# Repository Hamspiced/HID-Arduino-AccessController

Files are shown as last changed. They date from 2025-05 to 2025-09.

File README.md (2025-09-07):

# HID-Arduino-AccessController
This is a project repository for creating a full fledged door access controller using an HID Reader, Arduino, and i2c screen.  

The Arduino portion of this project will allow you to use the reader as a simple badge scanner, act as a door controller, identify authorized access control cards, add cards, and delete cards.

The ESP32 Portion of this project will do all of the same as well as connect to your wifi or host an AP that can be connected do.  Through the Web Server you can add an Admin card, trigger the door signal, add cards, remove cards, as well as see a log of all scanned cards.

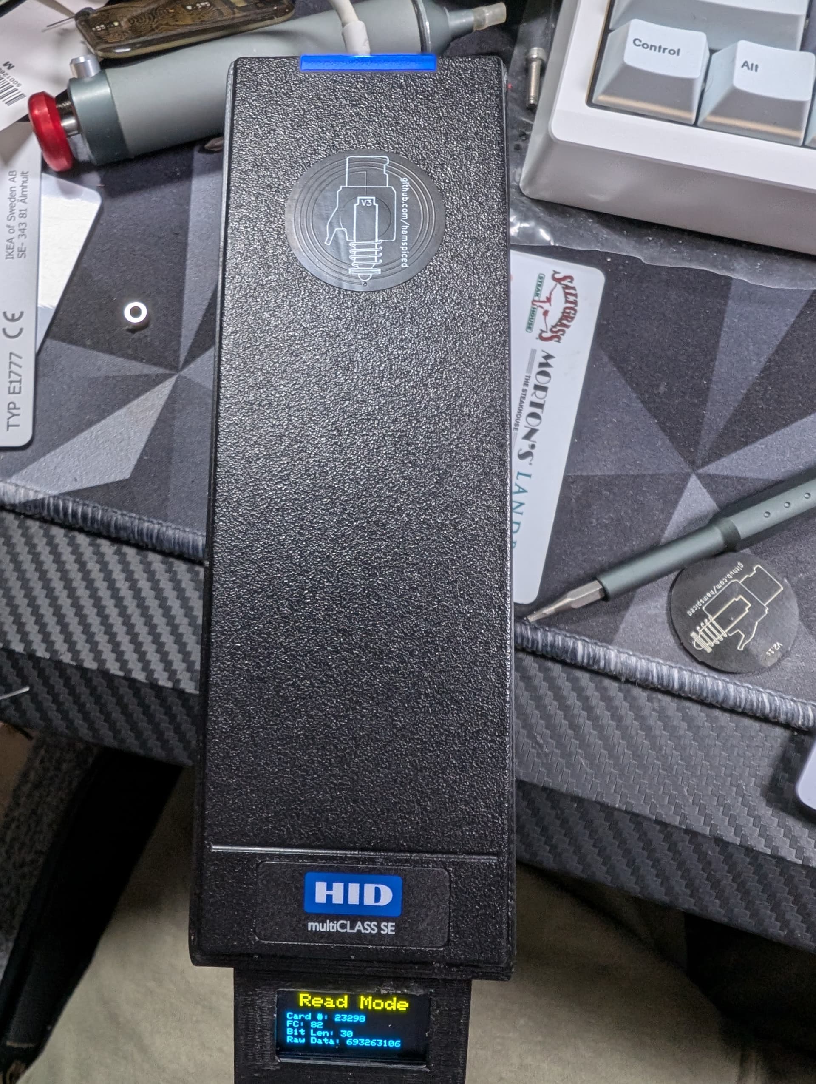
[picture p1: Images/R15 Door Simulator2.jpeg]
R15 Door Simulator


## Parts

 [Arduino Nano](https://a.co/d/4Q9VMcR) - $16.49 per 3 or $5.49 ea
 or
 [Esp32 Dev board](https://a.co/d/32qhvlW) - $29 for 5 or 5.50$ each
 
 [USB-C Pigtail](https://a.co/d/i3n7h48) - $7.99 per 10 or $0.80 ea
 
 [Arduino Breakout Board](https://a.co/d/hGXZX4y) - $8.79 per 3 or $2.93 ea
 
 [5v Buck Converter](https://a.co/d/7Qql78y) - $11.59 per 5 or $2.32 ea
 
 [i2c 2 Color OLED](https://a.co/d/0r9uNRJ) - $13.98 per 5 or $2.80 ea
 
 HID R10 or R15 Multiclass Reader - Ebay or Marketplace Price Varies between 20-90$ Any reader should work that uses the Wiegand protocol

Total Cost without Reader: $58.84/$14.34

Optional (if you want to add a Relay and Door Striker/Mag Lock

 [DC 5v Relay Module 1 Channel](https://a.co/d/gpslT7C) - 12.99 per $10 or $1.29 ea
 
 [USB-C PD Trigger Board](https://a.co/d/3NxkBei) $9.98 for 4 or $2.50 ea
 
 [12v Door Strike](https://a.co/d/8t9gDx0) $64.19 each
 
 [12v Pin Deadbolt (used in my Test Bench)](https://www.aliexpress.us/item/3256804840295067.html) $10.00 each

## 3d Printed Cases

 I have the cases uploaded to Thingiverse but in case it goes down ill attach them to the repository.  Ive made 2 cases for the two different form factors of the Rp15 and 
 R10 Multiclass Se Readers 
 
 [RP15 Case STL - Top](https://github.com/Hamspiced/HID-Arduino-AccessController/blob/main/Cases/R15_Bottom.stl)
 
 [RP15 Case STL - Bottom](https://github.com/Hamspiced/HID-Arduino-AccessController/blob/main/Cases/R15__Top.stl)
 
 [R10 Case STL - Top](https://github.com/Hamspiced/HID-Arduino-AccessController/blob/main/Cases/R10_Case_Top.stl)
 
 [R10 Case STL - Bottom](https://github.com/Hamspiced/HID-Arduino-AccessController/blob/main/Cases/R10_Case_bottom.stl)
 
 [R10 Case with MagLock STL - Top](https://github.com/Hamspiced/HID-Arduino-AccessController/blob/main/Cases/R10_MaglockCase_Top.stl)
 
 [R10 Case With Maglock STL - Bottom](https://github.com/Hamspiced/HID-Arduino-AccessController/blob/main/Cases/R10_MaglockCase_bottom.stl)

## 📌 ARDUINO Pinout Connections

### 🔌 HID Reader to Arduino Uno

| HID Wire Color | Arduino Uno Pin |
|---|---|
| Black | GND |
| Green | D2 |
| White | D3 |
| Brown | D5 |
| Orange | D6 |
| Yellow | A3 |

### 📟 OLED to Arduino

| OLED Pin | Arduino Uno Pin |
|---|---|
| VCC | 5V |
| GND | GND |
| SCL | A5 |
| SDA | A4 |

### ⚡ Power Input to Step-Down Converter

| Power Input Wire | Step-Down Pin |
|---|---|
| Black | - IN |
| Red | + IN |

### 🔋 Step-Down Converter to Arduino

| Step-Down Pin | Arduino Uno Pin |
|---|---|
| - OUT | GND |
| + OUT | VIN |

 Note: Match the Pins to the pin on that actual microcontroller and not to the printed labels on the breakout board.

## Assembly
 Next assemble the OLED into the case, you may need a dab of hot glue to secureit. 
 Attach the Readerto the case next its easiest to keep the base plate on and thread the screws down from the reader into the case and use nuts to secure the case to the reader and trim off excess of the screw.
 attach the breakout board to the bottom case
 attach MCU to the breakout board.  
 Stepdown module can go in its slot and it should clip into place.  
 Feed the wires for the pig tail USB C into the case from outside and press fit into place, then solder the connection to the stepdown converter In + and -
 You can use Heatset inserts or just screws to attach to the bottom of the case.

Note: When programming you have to connect USB C directly to the arduino, The USB-C Pigtail is power only it wont pass data through so you cant update your Arduino with this connection.  Likewise you cannot power the reader directly by the Arduino power, it isnt poweful enough for that.

## Assembly of Relay + Door Strike.
Run Wire from Arduino Pin 7 or ESP32 Pin 27 to Relay IN 
Run 12v+ from USB-C PD to Door Strike
Run 12v- from USB-C PD to Relay Com.
Run Wire from NO (Normall Open) on Relay to Doorstrike.
Run 5v+ From Step Down to DC+ on relay
Run 5v- from Step Down to DC- on relay

# Flashing Arduino via Arduino IDE

Download and install Arduino IDE.
You can copy the code file itself, or copy and paste the code into IDE.  Some MCU's from china require you to select old bootloader, or power up while pressing the reset button. 

# Use
On Startup the Reader defaults to Read Mode.  To switch modes you will need to pre-program 4 cards or add your card UID to the code  by default it is:

### 🏷️ RFID Mode UIDs and Proxmark3 Commands

| Mode | UID | LF Command (T5577) | HF Command (Magic 1K Card) |
|---|---|---|---|
| Read Mode | `0x1E6DC032` | `lf em 410xwrite 1E6DC032` | `hf mf csetuid -u 1E6DC032` |
| Door Mode | `0x1E6D9861` | `lf em 410xwrite 1E6D9861` | `hf mf csetuid -u 1E6D9861` |
| Add Mode | `0x1E6DFCA0` | `lf em 410xwrite 1E6DFCA0` | `hf mf csetuid -u 1E6DFCA0` |
| Remove Mode  | `0x1E6DE636` | `lf em 410xwrite 1E6DE636` | `hf mf csetuid -u 1E6DE636` |

Door Mode will send a Signal on Pin6 to activate a Door Relay when authorized cards are scanned.
When Add Mode is selected, when a card is scanned it is added to the controller
when Remove mode is selected if that card is scanned it is removed from the controller

TODO: Scanning the remove mode card 3 times will reset all added cards (not mode cards)

# Configuring the Admin UID (Arduino Nano)

The Arduino Nano build uses an Admin card to cycle modes (READ → DOOR → ADD → DEL). To set your own Admin UID:

1) Get your card's UID
- Put the Nano in READ MODE and scan the card. The OLED shows the HEX UID as “Card: 0x…”. Convert that HEX to decimal, or temporarily enable Serial to print the decimal (see step 2).

2) Optional: enable Serial to view the decimal UID
- In `Arduino nano Code/HIDR10-RP15-Door-Simulator/HIDR10-RP15-Door-Simulator.ino`, set `#define ENABLE_SERIAL 1`. Upload, open Serial Monitor at 115200, scan the card, note the `RAW` decimal, then set `ENABLE_SERIAL` back to 0 if desired.

3) Set the Admin UID
- In the same file, edit the line:
  `#define ADMIN_UID_DEFAULT 253411519UL`
  Replace `253411519UL` with your card's decimal UID and keep the `UL` suffix.

4) Upload the sketch
- Upload to your Nano. On boot, the Admin UID will be used to detect admin scans and cycle modes.

Notes
- The Admin UID is read from EEPROM if present; when EEPROM is blank, the compiled `ADMIN_UID_DEFAULT` is used. If you later change the default and re-upload, the new default will take effect without any extra steps.

# ESP32 Installation

I use Arduino IDE for the ESP32.  I had to download the ESP32Little Fs plugin for Arduino IDE 2.x.   More information on it can be found from [earlephilhower's Github](https://github.com/earlephilhower/arduino-littlefs-upload) the TL;DR is: 

Copy the VSIX file to ~/.arduinoIDE/plugins/ on Mac and Linux or C:\Users\<username>\.arduinoIDE\plugins\ on Windows (you may need to make this directory yourself beforehand).

Once the plugin is in it's folder.  You can load the INO file into your sketch.  In the sketch folder, in the root create a directory called "data" and place the html file in there.  Then, Upload your code to your ESP32 (selecting the proper board and port).  When upload is complete: 

On Windows: press [Ctrl] + [Shift] + [P], then "Upload LittleFS to Pico/ESP8266/ESP32".

On macOS: press [⌘] + [Shift] + [P] to open the Command Palette in the Arduino IDE, then "Upload LittleFS to Pico/ESP8266/ESP32".

It will upload the data folder with the web page interface.

  ## ESP32 Usage

The ESP32 adds a Web Interface to the RFID Reader.  It will allow you to access a webpage (192.168.4.1 when in Access Point Mode) that will allow you to add Admin Cards, Trigger the door sensor, and display a card log.  

  ##REST Api

  There are Endpoints for the REST API already added to the code.  The Endpoint webhooks are within the code.  I dont use Home Assistant but if you are savvy you should be able to use this with home assistant.

## Pinouts for ESP32 devices
   
   ### 📌 Xiao ESP32C3 Pin Mapping

   | Function      | Physical Pin | Arduino Pin |
   |---------------|--------------|-------------|
   | Wiegand D0    | 2            | D2          |
   | Wiegand D1    | 3            | D3          |
   | Beeper        | 6            | D6          |
   | Door Strike   | 7            | D7          |
   | I2C SDA       | 4            | D4          |
   | I2C SCL       | 5            | D5          |

   ### 📌  ESP32 Pin Mapping

   | Function      | GPIO         | Label          |
   |---------------|--------------|----------------|
   | Wiegand D0    | 16           | Wiegand D0 Pin |
   | Wiegand D1    | 17           | Wiegand D1 Pin |
   | Beeper        | 26           | Beeper Pin     |
   | Door Strike   | 27           | Signal Pin     |
   | I2C SDA       | 21           | SSD1306 OLED   |
   | I2C SCL       | 22           | SSD1306 OLED   |

 # Use

 When booted up the esp32 will broadcast a Wifi Signal named: Door-Simulator.  Encryption Key is "12345678".  In the code you can also specify your own wifi network for it to connect to.  By default the default AP will host the webservice on: 192.168.4.1

# Home Assistant Integration Guide

## 1. Install a Text Editor Add-on

- Install a **Text Editor Add-on** or **Studio Code Server Add-on** from the Home Assistant Add-on Store.

## 2. Edit Configuration

- Open your `configuration.yaml` file with your preferred editor.
- Paste the contents of **RFIDHomeAssistant.yaml** at the **end** of your `configuration.yaml`.
- **Important:** Change `"YourDeviceIPaddress"` to the static IP assigned to your door reader.

## 3. Check and Restart

- Go to **Developer Tools** → **YAML** → **Check Configuration**.
- If the configuration is valid, press **Restart**. (You may need to confirm a few times.)

## 4. Verify Entities

After restart, go to:

    Settings > Devices & Services > Entities

Search for:

- `sensor.rfid_door_mode`
- `sensor.rfid_last_card`

These entities will show the current mode and the last card scanned.

---

## 5. Trigger Door

- Go to **Developer Tools** → **Services**.
- Search for `rest_command.trigger_rfid_door` and click **Call Service** to test.

---

## 6. Change Mode

- Use `rest_command.set_rfid_mode` with a data payload to set the desired mode.

---

## Add the New Entities to Your Dashboard

1. Go to your dashboard.
2. Click the three dots (⋮) in the upper right and choose **Take Control**.
3. Click **Add Card** in the lower right.
4. Choose **By Entity**.
5. Select the RFID entities and hit **Continue**.

---

## Add a Mode Button

You can also add a button to display and control the reader mode:

```yaml
type: button
entity: sensor.rfid_door_mode
name: RFID Mode
show_state: true
tap_action:
  action: call-service
  service: rest_command.cycle_rfid_mode
```   

## 🙏 Acknowledgments

Huge thanks to [Peekaboo](https://github.com/Peekaboo-ICU) for their invaluable support in helping bring this project to life.  
From debugging my bad code to offering key insights and improvements, their contributions were instrumental in getting this over the finish line.  

Explore more of their work at [Peekaboo.icu](https://peekaboo.icu)

## License

This project is licensed under the [Creative Commons Attribution-NonCommercial 4.0 International (CC BY-NC 4.0)](https://creativecommons.org/licenses/by-nc/4.0/).

You are free to use, modify, and share this code for **non-commercial purposes**, provided proper attribution is given.  
**Commercial use is not permitted** without prior written consent. Please [contact the author](mailto:your.email@example.com) to inquire about commercial licensing.

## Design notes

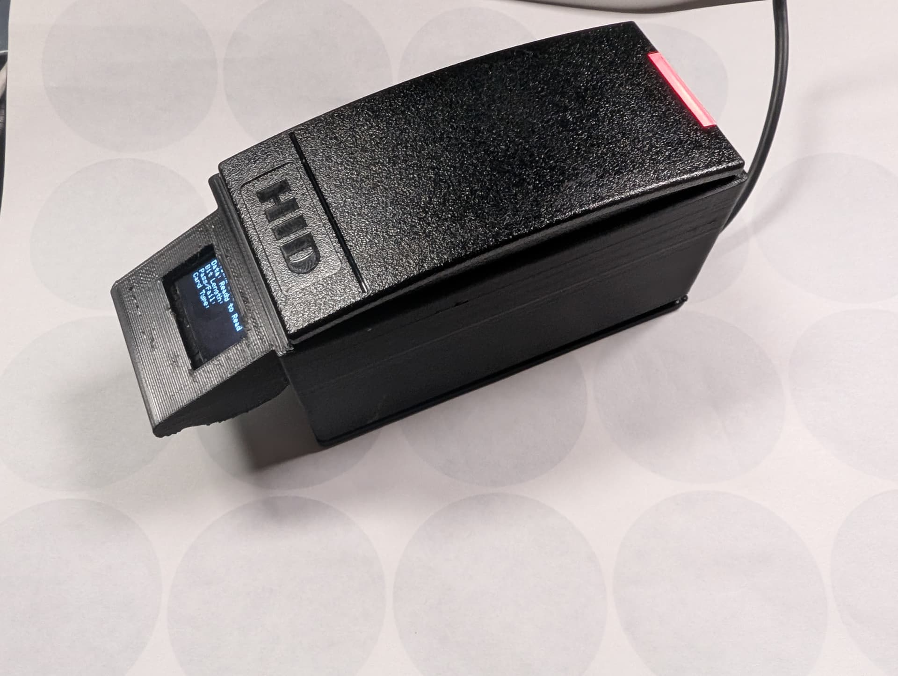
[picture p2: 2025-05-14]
Images/Rp10 Door Simulator.jpeg

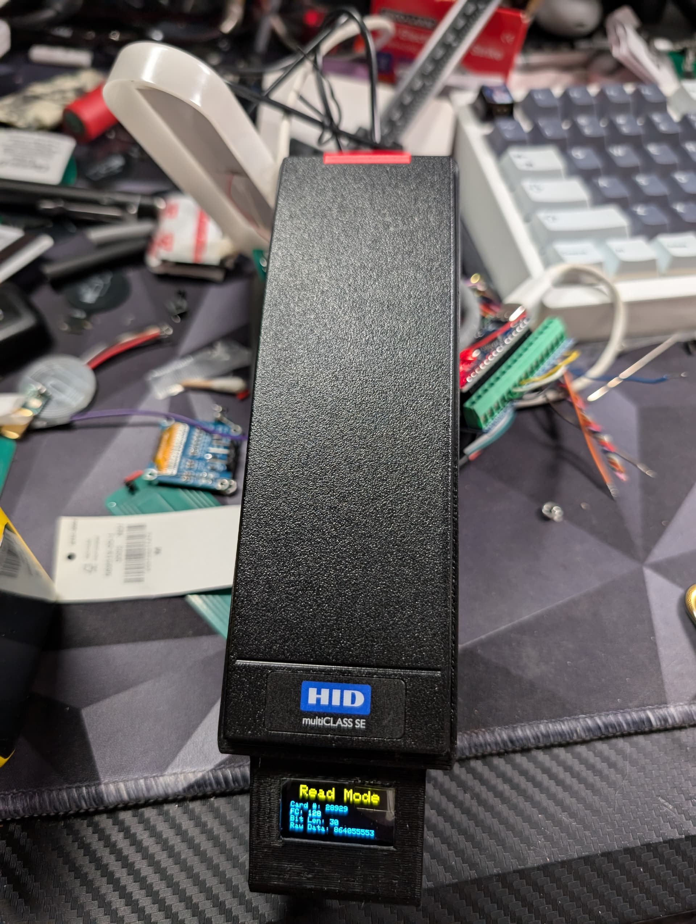
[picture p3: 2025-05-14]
Images/R15 Door Simulator.jpeg

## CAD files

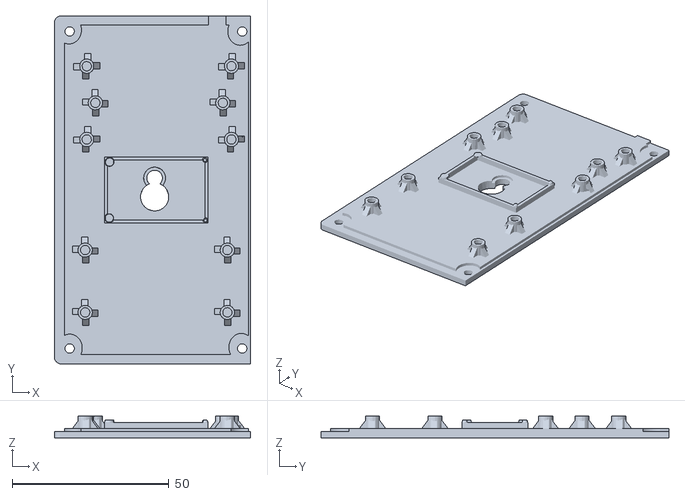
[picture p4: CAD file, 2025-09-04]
Cases/R10_MaglockCase_bottom.stl
62.6 x 111.0 x 6.90

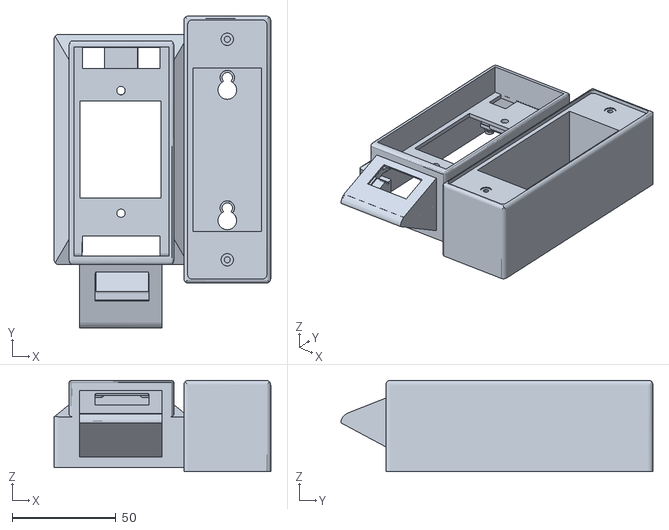
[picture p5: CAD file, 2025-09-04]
Cases/R10_MaglockCase_top.stl
104.6 x 150.7 x 44.0

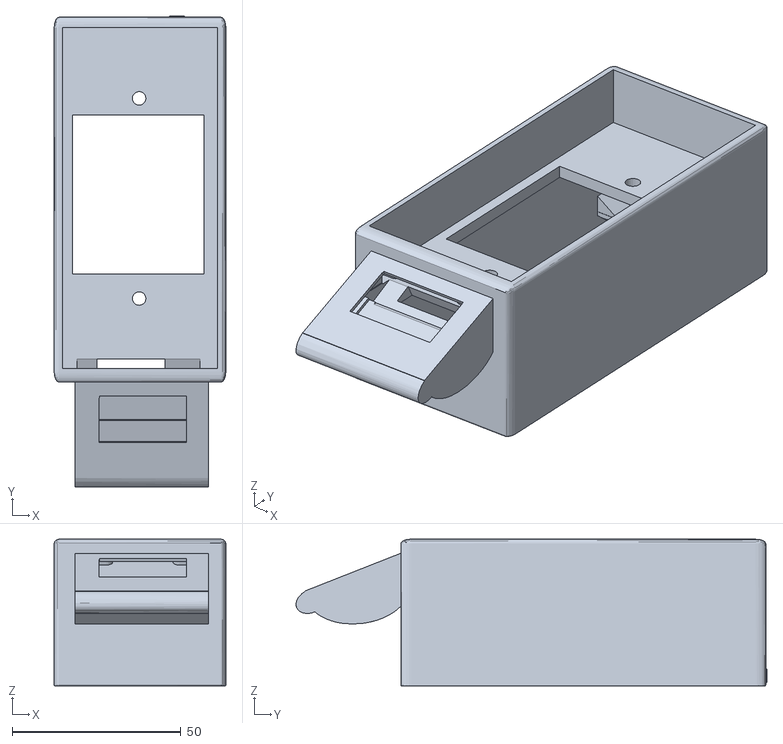
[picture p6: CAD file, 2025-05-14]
Cases/R10_Case_Top.stl
50.8 x 139.4 x 43.4

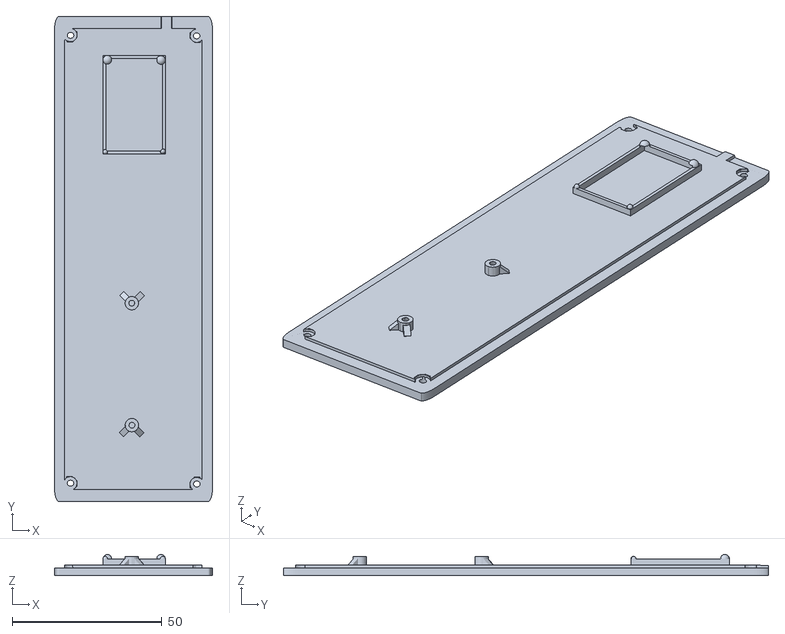
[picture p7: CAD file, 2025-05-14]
Cases/Rp15_Bottom.stl
52.8 x 162.0 x 7.06

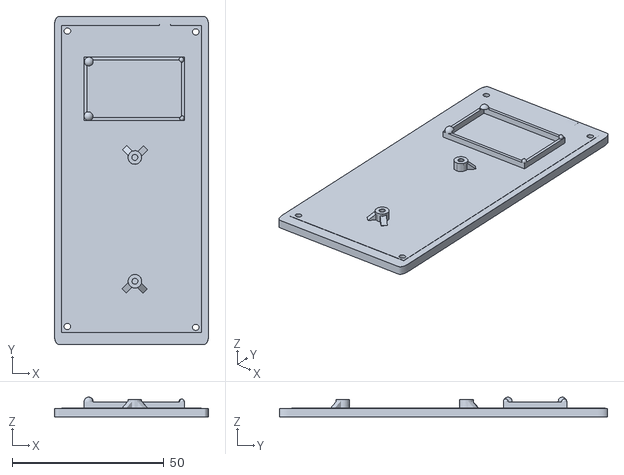
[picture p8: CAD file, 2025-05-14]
Cases/R10_Case_bottom.stl
50.8 x 107.9 x 6.50

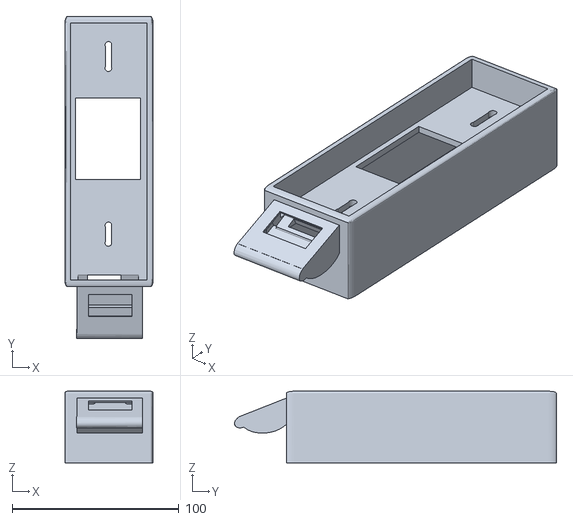
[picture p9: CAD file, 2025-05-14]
Cases/Rp15_Top.stl
53.0 x 193.0 x 42.9

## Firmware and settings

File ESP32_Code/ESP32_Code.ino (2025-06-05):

#include <Arduino.h>
#include <WiFi.h>
#include <WebServer.h>
#include <LittleFS.h>
#include <Wire.h>
#include <Adafruit_GFX.h>
#include <Adafruit_SSD1306.h>
#include <Wiegand.h>

#define SCREEN_WIDTH 128
#define SCREEN_HEIGHT 64
#define OLED_RESET    -1
#define SCREEN_ADDRESS 0x3C

#define WIEGAND_D0_PIN 16
#define WIEGAND_D1_PIN 17
#define BEEPER_PIN     26
#define SIGNAL_PIN     27

// --- Wi-Fi and Static IP Configuration ---
//Put your SSID in here Below
String userSSID = "YourSSID";
//Put your Password for your SSID below
String userPassword = "YourWifiAddress";
bool useHardcodedIP = true; // Set to true to use static IP below
IPAddress hardcodedIP(192, 168, 1, 100);
IPAddress hardcodedGW(192, 168, 1, 1);
IPAddress hardcodedSN(255, 255, 255, 0);

const char* ap_ssid = "RFID-Door-Sim";
const char* ap_password = "12345678";

const unsigned long ADMIN_UID = 562141196;

WebServer server(80);
WIEGAND wg;
Adafruit_SSD1306 display(SCREEN_WIDTH, SCREEN_HEIGHT, &Wire, OLED_RESET);

#define MAX_CARDS 20
#define CARD_SIZE sizeof(unsigned long)
const char* cardsFile = "/cards.txt";
const char* logFile = "/scanlog.txt";

unsigned long authorizedCards[MAX_CARDS];
uint8_t cardCount = 0;

#define MODE_READ   1
#define MODE_DOOR   2
#define MODE_ADD    3
#define MODE_REMOVE 4

uint8_t currentMode = MODE_READ;
unsigned long lastCardData = 0;
uint8_t lastBitLength = 0;
uint8_t lastFacilityCode = 0;
uint16_t lastCardNumber = 0;

#define MODE_CARD_READ   0x1E6DC032
#define MODE_CARD_DOOR   0x1E6D9861
#define MODE_CARD_ADD    0x1E6DFCA0
#define MODE_CARD_REMOVE 0x1E6DE636

const unsigned long configCards[4] = {
  MODE_CARD_READ,
  MODE_CARD_DOOR,
  MODE_CARD_ADD,
  MODE_CARD_REMOVE
};

unsigned long parseCard(String line) {
  return strtoul(line.c_str(), NULL, 10);
}

void loadAuthorizedCards() {
  cardCount = 0;
  if (!LittleFS.exists(cardsFile)) return;

  File file = LittleFS.open(cardsFile, "r");
  while (file.available() && cardCount < MAX_CARDS) {
    String line = file.readStringUntil('\n');
    authorizedCards[cardCount++] = parseCard(line);
  }
  file.close();
}

void saveAuthorizedCards() {
  File file = LittleFS.open(cardsFile, "w");
  for (uint8_t i = 0; i < cardCount; i++) {
    file.println(String(authorizedCards[i]));
  }
  file.close();
}

bool isAuthorized(unsigned long cardData) {
  for (uint8_t i = 0; i < cardCount; i++) {
    if (authorizedCards[i] == cardData) return true;
  }
  return false;
}

void addCard(unsigned long cardData) {
  if (cardCount < MAX_CARDS && !isAuthorized(cardData)) {
    authorizedCards[cardCount++] = cardData;
    saveAuthorizedCards();
  }
}

void removeCard(unsigned long cardData) {
  for (uint8_t i = 0; i < cardCount; i++) {
    if (authorizedCards[i] == cardData) {
      for (uint8_t j = i; j < cardCount - 1; j++) {
        authorizedCards[j] = authorizedCards[j + 1];
      }
      cardCount--;
      saveAuthorizedCards();
      break;
    }
  }
}

String modeName(uint8_t mode) {
  switch (mode) {
    case MODE_READ: return "READ MODE";
    case MODE_DOOR: return "DOOR MODE";
    case MODE_ADD: return "ADD MODE";
    case MODE_REMOVE: return "DEL MODE";
    default: return "UNKNOWN";
  }
}

String getCardJSON() {
  String json = "{";
  json += "\"mode\":\"" + modeName(currentMode) + "\",";
  json += "\"card\":\"0x" + String(lastCardData, HEX) + "\",";
  json += "\"fc\":\"" + String(lastFacilityCode) + "\",";
  json += "\"id\":\"" + String(lastCardNumber) + "\"";
  json += "}";
  return json;
}

void handleRoot() {
  File file = LittleFS.open("/index.html", "r");
  if (!file) {
    server.send(500, "text/plain", "index.html missing");
    return;
  }
  server.streamFile(file, "text/html");
  file.close();
}

void handleStatus() {
  server.send(200, "application/json", getCardJSON());
}

void handleSetMode() {
  if (server.hasArg("admin")) {
    unsigned long adminCard = strtoul(server.arg("admin").c_str(), NULL, 10);
    if (adminCard == ADMIN_UID) {
      currentMode++;
      if (currentMode > MODE_REMOVE) currentMode = MODE_READ;
      server.send(200, "text/plain", "Admin card cycled mode.");
      return;
    } else {
      File f = LittleFS.open("/admin.txt", "w");
       if (f) {
       f.println(String(adminCard));
       f.close();
       server.send(200, "text/plain", "Admin card saved.");
       } else {
       server.send(500, "text/plain", "Failed to save admin card.");
       }
      return;
    }
  }
  
  if (server.hasArg("m")) {
    uint8_t mode = server.arg("m").toInt();
    if (mode >= MODE_READ && mode <= MODE_REMOVE) {
      currentMode = mode;
    }
  } else if (server.hasArg("scan")) {
    unsigned long scannedCard = strtoul(server.arg("scan").c_str(), NULL, 16);
    for (uint8_t i = 0; i < 4; i++) {
      if (scannedCard == configCards[i]) {
        currentMode = i + 1;
        break;
      }
    }
  }
  displayScanPrompt();  // ✅ Add this line here to update OLED
  server.send(200, "text/plain", "Mode Set");
}

void handleTriggerDoor() {
  digitalWrite(SIGNAL_PIN, HIGH);
  delay(5000);
  digitalWrite(SIGNAL_PIN, LOW);
  server.send(200, "text/plain", "Triggered");
}

// --- REST API Endpoints ---

void handleApiStatus() {
  server.send(200, "application/json", getCardJSON());
}

void handleApiCardsGet() {
  String json = "[";
  for (uint8_t i = 0; i < cardCount; i++) {
    json += String(authorizedCards[i]);
    if (i < cardCount - 1) json += ",";
  }
  json += "]";
  server.send(200, "application/json", json);
}

void handleApiCardsPost() {
  if (!server.hasArg("card")) {
    server.send(400, "application/json", "{\"error\":\"Missing card\"}");
    return;
  }
  unsigned long cardData = strtoul(server.arg("card").c_str(), NULL, 10);
  addCard(cardData);
  server.send(200, "application/json", "{\"success\":true}");
}

void handleApiCardsDelete() {
  if (!server.hasArg("card")) {
    server.send(400, "application/json", "{\"error\":\"Missing card\"}");
    return;
  }
  unsigned long cardData = strtoul(server.arg("card").c_str(), NULL, 10);
  removeCard(cardData);
  server.send(200, "application/json", "{\"success\":true}");
}

void handleApiTrigger() {
  digitalWrite(SIGNAL_PIN, HIGH);
  delay(5000);
  digitalWrite(SIGNAL_PIN, LOW);
  server.send(200, "application/json", "{\"success\":true}");
}

void handleApiModePost() {
  if (!server.hasArg("mode")) {
    server.send(400, "application/json", "{\"error\":\"Missing mode\"}");
    return;
  }
  uint8_t mode = server.arg("mode").toInt();
  if (mode >= MODE_READ && mode <= MODE_REMOVE) {
    currentMode = mode;
    displayScanPrompt();
    server.send(200, "application/json", "{\"success\":true}");
  } else {
    server.send(400, "application/json", "{\"error\":\"Invalid mode\"}");
  }
}

void handleApiLogGet() {
  File log = LittleFS.open(logFile, "r");
  if (!log) {
    server.send(200, "application/json", "{\"error\":\"Log file not found.\"}");
    return;
  }
  String logData;
  while (log.available()) {
    logData += log.readStringUntil('\n') + "\\n";
  }
  log.close();
  server.send(200, "text/plain", logData);
}

// --- Webserver ---

void setupWebServer() {
  server.on("/", handleRoot);
  server.on("/status", handleStatus);
  server.on("/mode", handleSetMode);
  server.on("/trigger", handleTriggerDoor);
  server.on("/log", handleLogFile);
  server.on("/wifi", HTTP_POST, []() {
    if (server.hasArg("ssid") && server.hasArg("pass")) {
      String newSSID = server.arg("ssid");
      String newPASS = server.arg("pass");
      String newIP = server.hasArg("ip") ? server.arg("ip") : "";
      String newGW = server.hasArg("gw") ? server.arg("gw") : "";
      String newSN = server.hasArg("subnet") ? server.arg("subnet") : "";

      File config = LittleFS.open("/wifi.txt", "w");
      config.println(newSSID);
      config.println(newPASS);
      config.println(newIP);
      config.println(newGW);
      config.println(newSN);
      config.close();

      server.send(200, "text/plain", "Wi-Fi settings saved. Please reboot.");
    } else {
      server.send(400, "text/plain", "Missing SSID or Password");
    }
  });

// --- REST API Endpoints ---
server.on("/api/status", HTTP_GET, handleApiStatus);
server.on("/api/cards", HTTP_GET, handleApiCardsGet);
server.on("/api/cards", HTTP_POST, handleApiCardsPost);
server.on("/api/cards", HTTP_DELETE, handleApiCardsDelete);
server.on("/api/trigger", HTTP_POST, handleApiTrigger);
server.on("/api/mode", HTTP_POST, handleApiModePost);
server.on("/api/log", HTTP_GET, handleApiLogGet);

//	•	Get status: GET http://esp32.local/api/status
//	•	Add card: POST http://esp32.local/api/cards with body card=123456
//	•	Remove card: DELETE http://esp32.local/api/cards?card=123456
//	•	Trigger door: POST http://esp32.local/api/trigger
//	•	Set mode: POST http://esp32.local/api/mode with body mode=1
//	•	Get log: GET http://esp32.local/api/log

  // ✅ Start the web server AFTER all routes are defined
  server.begin();
}

void connectWiFi() {
  WiFi.mode(WIFI_AP_STA);
  String ssidVal = userSSID;
  String passVal = userPassword;
  IPAddress local_IP, gateway, subnet;

  if (useHardcodedIP) {
    WiFi.config(hardcodedIP, hardcodedGW, hardcodedSN);
  } else if (LittleFS.exists("/wifi.txt")) {
    File f = LittleFS.open("/wifi.txt", "r");
    ssidVal = f.readStringUntil('\n');
    passVal = f.readStringUntil('\n');
    String ip = f.readStringUntil('\n');
    String gw = f.readStringUntil('\n');
    String sn = f.readStringUntil('\n');
    ssidVal.trim(); passVal.trim();
    ip.trim(); gw.trim(); sn.trim();
    f.close();

    if (ip.length() && gw.length() && sn.length()) {
      if (local_IP.fromString(ip) && gateway.fromString(gw) && subnet.fromString(sn)) {
        WiFi.config(local_IP, gateway, subnet);
      }
    }
  }

  WiFi.begin(ssidVal.c_str(), passVal.c_str());
  unsigned long start = millis();
  while (WiFi.status() != WL_CONNECTED && millis() - start < 10000) {
    delay(100);
  }

  if (WiFi.status() == WL_CONNECTED) {
    Serial.println("Connected to WiFi");
    Serial.println(WiFi.localIP());
  } else {
    WiFi.softAP(ap_ssid, ap_password);
    Serial.println("Started Access Point");
    Serial.println(WiFi.softAPIP());
  }
}

unsigned long loadAdminUID() {
  if (LittleFS.exists("/admin.txt")) {
    File f = LittleFS.open("/admin.txt", "r");
    if (f) {
      String line = f.readStringUntil('\n');
      f.close();
      return strtoul(line.c_str(), NULL, 10);
    }
  }
  return 0;
}

void displayScanPrompt() {
  display.clearDisplay();
  display.setTextSize(2);
  display.setCursor(0, 0);
  display.println(modeName(currentMode));
  display.setTextSize(1);
  display.setCursor(0, 20);
  display.println("Scan Card to Begin...");
  display.display();
}

void setup() {
  WiFi.mode(WIFI_AP_STA);
  WiFi.softAP(ap_ssid, ap_password);
  Serial.begin(115200);
  Serial.println("STA IP: " + WiFi.localIP().toString());
  Serial.println("AP IP: " + WiFi.softAPIP().toString());

  if (!LittleFS.begin()) {
    Serial.println("LittleFS mount failed");
    return;
  }
  if (LittleFS.exists("/index.html")) {
  Serial.println("index.html found on LittleFS.");
    } else {
    Serial.println("index.html MISSING on LittleFS.");
    }
  display.begin(SSD1306_SWITCHCAPVCC, SCREEN_ADDRESS);
  display.clearDisplay();
  display.setTextColor(SSD1306_WHITE);
  display.setTextSize(2);
  display.setCursor(18, 0);
  display.println("READ MODE");
  display.setTextSize(1); 
  display.setCursor(0, 20);
  display.println("Scan Card to Begin...");
  display.display();

    String cardType = (wg.getWiegandType() == 26) ? "Wiegand26" : "Unknown";
    appendLogEntry(lastCardData, lastFacilityCode, lastCardNumber, cardType);
  delay(1000);

  pinMode(BEEPER_PIN, OUTPUT);
  digitalWrite(BEEPER_PIN, HIGH);
  pinMode(SIGNAL_PIN, OUTPUT);
  digitalWrite(SIGNAL_PIN, LOW);

  wg.begin(WIEGAND_D0_PIN, WIEGAND_D1_PIN);
  loadAuthorizedCards();
  connectWiFi();
  configTime(0, 0, "pool.ntp.org");
  setupWebServer();
  }

void loop() {
  server.handleClient();

  if (wg.available()) {
    unsigned long cardData = wg.getCode();
    unsigned long adminUID = loadAdminUID();
    if (cardData == adminUID) {
      currentMode++;
      if (currentMode > MODE_REMOVE) currentMode = MODE_READ;
      displayScanPrompt();
      return;
    }
    lastCardData = cardData;
    lastBitLength = 0;
    unsigned long data = lastCardData;
    while (data) { lastBitLength++; data >>= 1; }

    lastFacilityCode = (lastCardData >> 16) & 0xFF;
    lastCardNumber = lastCardData & 0xFFFF;

    digitalWrite(BEEPER_PIN, LOW);
    delay(50);
    digitalWrite(BEEPER_PIN, HIGH);

    display.clearDisplay();
    display.setTextSize(2);
    display.setCursor(0, 0);
    display.println(modeName(currentMode));

    display.setTextSize(1);
    display.setCursor(0, 20);
    display.print("Card: 0x");
    display.println(lastCardData, HEX);

    display.setCursor(0, 30);
    display.print("Facility: ");
    display.println(lastFacilityCode);

    display.setCursor(0, 40);
    display.print("ID: ");
    display.println(lastCardNumber);

    switch (currentMode) {
      case MODE_READ:
        Serial.printf("Card: 0x%08lX\n", lastCardData);
        // No change to display or logging in READ mode
        break;

      case MODE_DOOR: {
        // Check authorization and display result
        bool authorized = isAuthorized(lastCardData);

        display.setTextSize(2);
        display.setCursor(0, 50); // Lower part of OLED
        if (authorized) {
          display.println("AUTHORIZED");
          digitalWrite(SIGNAL_PIN, HIGH);
          delay(5000);
          digitalWrite(SIGNAL_PIN, LOW);
        } else {
          display.println("NO ENTRY");
          // Door is not triggered
        }
        display.display();

        // Log every scan in DOOR MODE (authorized or not)
        String cardType = (wg.getWiegandType() == 26) ? "Wiegand26" : "Unknown";
        appendLogEntry(lastCardData, lastFacilityCode, lastCardNumber, cardType);

        break;
      }

      case MODE_ADD:
        addCard(lastCardData);
        break;
      case MODE_REMOVE:
        removeCard(lastCardData);
        break;
    }

    // In READ mode and others, keep your existing display logic
    if (currentMode != MODE_DOOR) {
      display.display();
    }

    // Log card in modes other than DOOR if needed (existing logic)
    if (currentMode != MODE_DOOR) {
      String cardType = (wg.getWiegandType() == 26) ? "Wiegand26" : "Unknown";
      appendLogEntry(lastCardData, lastFacilityCode, lastCardNumber, cardType);
    }
  }
}

String getTimestamp() {
  time_t now = time(nullptr);
  struct tm* t = localtime(&now);
  char buf[64];
  snprintf(buf, sizeof(buf), "%04d-%02d-%02d %02d:%02d:%02d",
           t->tm_year + 1900, t->tm_mon + 1, t->tm_mday,
           t->tm_hour, t->tm_min, t->tm_sec);
  return String(buf);
}

void appendLogEntry(unsigned long raw, uint8_t fc, uint16_t id, String type) {
  File log = LittleFS.open(logFile, "a");
  if (log) {
    log.printf("%s | RAW: %lu | FC: %u | ID: %u | TYPE: %s\n",
               getTimestamp().c_str(), raw, fc, id, type.c_str());
    log.close();
  }
}

void handleLogFile() {
  File log = LittleFS.open(logFile, "r");
  if (!log) {
    server.send(200, "text/plain", "Log file not found.");
    return;
  }

  server.streamFile(log, "text/plain");
  log.close();
}

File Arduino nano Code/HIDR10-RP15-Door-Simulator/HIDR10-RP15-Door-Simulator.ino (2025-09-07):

#include <Wire.h>
#include <Adafruit_GFX.h>
#include <Adafruit_SSD1306.h>
#include <Wiegand.h>
#include <EEPROM.h>

#define SCREEN_WIDTH 128
#define SCREEN_HEIGHT 64
#define OLED_RESET -1
#define SCREEN_ADDRESS 0x3C

#define WIEGAND_D0_PIN 2 // Green wire (Data 0)
#define WIEGAND_D1_PIN 3 // White wire (Data 1)
#define BEEPER_PIN A3
#define SIGNAL_PIN 7 // Door strike signal pin

#define MAX_CARDS 20
#define EEPROM_CARD_COUNT_ADDR 0
#define EEPROM_CARD_DATA_ADDR 4
#define CARD_SIZE sizeof(unsigned long)

#define ADMIN_UID_DEFAULT 253411519UL
#define EEPROM_ADMIN_UID_ADDR (EEPROM_CARD_DATA_ADDR + (MAX_CARDS * CARD_SIZE))

// Set to 0 to silence all Serial output
#define ENABLE_SERIAL 0

Adafruit_SSD1306 display(SCREEN_WIDTH, SCREEN_HEIGHT, &Wire, OLED_RESET);
WIEGAND wg;

bool cardDisplayed = false;
bool promptDisplayed = false;
unsigned long lastCardData = 0;
uint8_t lastBitLength = 0;
uint8_t lastFacilityCode = 0;
uint16_t lastCardNumber = 0;

#define MODE_READ 1
#define MODE_DOOR 2
#define MODE_ADD 3
#define MODE_REMOVE 4
uint8_t currentMode = MODE_READ;

unsigned long adminUID = ADMIN_UID_DEFAULT;

const unsigned long configCards[4] = {
  0x1E6DC032, // Read mode
  0x1E6D9861, // Door mode
  0x1E6DFCA0, // Add mode
  0x1E6DE636  // Remove mode
};

unsigned long authorizedCards[MAX_CARDS];
uint8_t cardCount = 0;

uint8_t countBits(uint32_t data) {
  uint8_t count = 0;
  while (data) {
    data >>= 1;
    count++;
  }
  return count;
}

void loadAuthorizedCards() {
  cardCount = EEPROM.read(EEPROM_CARD_COUNT_ADDR);
  if (cardCount > MAX_CARDS) {
    cardCount = 0;
    return;
  }
  for (uint8_t i = 0; i < cardCount; i++) {
    unsigned long cardData = 0;
    for (uint8_t j = 0; j < CARD_SIZE; j++) {
      cardData |= (unsigned long)EEPROM.read(EEPROM_CARD_DATA_ADDR + i * CARD_SIZE + j) << (8 * j);
    }
    authorizedCards[i] = cardData;
  }
}

void saveAuthorizedCards() {
  EEPROM.update(EEPROM_CARD_COUNT_ADDR, cardCount);
  for (uint8_t i = 0; i < cardCount; i++) {
    unsigned long cardData = authorizedCards[i];
    for (uint8_t j = 0; j < CARD_SIZE; j++) {
      EEPROM.update(EEPROM_CARD_DATA_ADDR + i * CARD_SIZE + j, (cardData >> (8 * j)) & 0xFF);
    }
  }
}

bool isAuthorized(unsigned long cardData) {
  for (uint8_t i = 0; i < cardCount; i++) {
    if (authorizedCards[i] == cardData) {
      return true;
    }
  }
  return false;
}

void addCard(unsigned long cardData) {
  if (cardCount < MAX_CARDS && !isAuthorized(cardData)) {
    authorizedCards[cardCount] = cardData;
    cardCount++;
    saveAuthorizedCards();
  }
}

void removeCard(unsigned long cardData) {
  for (uint8_t i = 0; i < cardCount; i++) {
    if (authorizedCards[i] == cardData) {
      for (uint8_t j = i; j < cardCount - 1; j++) {
        authorizedCards[j] = authorizedCards[j + 1];
      }
      cardCount--;
      saveAuthorizedCards();
      break;
    }
  }
}

const char* modeName(uint8_t mode) {
  switch (mode) {
    case MODE_READ:   return "READ MODE";
    case MODE_DOOR:   return "DOOR MODE";
    case MODE_ADD:    return "ADD MODE";
    case MODE_REMOVE: return "DEL MODE";
    default:          return "UNKNOWN";
  }
}

unsigned long loadAdminUID() {
  unsigned long uid = 0;
  for (uint8_t i = 0; i < 4; i++) {
    uid |= (unsigned long)EEPROM.read(EEPROM_ADMIN_UID_ADDR + i) << (8 * i);
  }
  if (uid == 0xFFFFFFFFUL || uid == 0UL) {
    return ADMIN_UID_DEFAULT;
  }
  return uid;
}

void saveAdminUID(unsigned long uid) {
  for (uint8_t i = 0; i < 4; i++) {
    EEPROM.update(EEPROM_ADMIN_UID_ADDR + i, (uid >> (8 * i)) & 0xFF);
  }
}

void appendLogEntry(unsigned long raw, uint8_t fc, uint16_t id) {
  #if ENABLE_SERIAL
  Serial.print("RAW: "); Serial.print(raw);
  Serial.print(" | HEX: 0x"); Serial.print(raw, HEX);
  Serial.print(" | FC: "); Serial.print(fc);
  Serial.print(" | ID: "); Serial.print(id);
  Serial.print(" | BITS: "); Serial.print(countBits(raw));
  Serial.print(" | TYPE: "); Serial.print(wg.getWiegandType() == 26 ? "Wiegand26" : "Unknown");
  Serial.print(" | t="); Serial.println(millis());
  #endif
}

void displayScanPrompt() {
  display.clearDisplay();
  display.setTextSize(2);
  display.setCursor(12, 0);
  switch (currentMode) {
    case MODE_READ:   display.println("READ MODE"); break;
    case MODE_DOOR:   display.println("DOOR MODE"); break;
    case MODE_ADD:    display.println("ADD MODE"); break;
    case MODE_REMOVE: display.println("DEL MODE"); break;
  }
  display.setTextSize(1);
  display.setCursor(0, 20);
  display.println("Scan Card to Begin...");
  display.display();
  cardDisplayed = false;
  promptDisplayed = true;
}

void displayCardData(unsigned long cardData, uint8_t bitLength, uint8_t facilityCode, uint16_t cardNumber, const char* message = "") {
  display.clearDisplay();
  display.setTextSize(2);
  display.setCursor(12, 0);
  switch (currentMode) {
    case MODE_READ:   display.println("READ MODE"); break;
    case MODE_DOOR:   display.println("DOOR MODE"); break;
    case MODE_ADD:    display.println("ADD MODE"); break;
    case MODE_REMOVE: display.println("DEL MODE"); break;
  }
  display.setTextSize(1);
  if (currentMode == MODE_READ) {
    display.setCursor(0, 20);
    display.print("Card: 0x");
    display.println(cardData, HEX);
    display.setCursor(0, 30);
    display.print("Facility: ");
    display.println(facilityCode);
    display.setCursor(0, 40);
    display.print("ID: ");
    display.println(cardNumber);
  } else {
    display.setCursor(30, 20); // Center message
    display.println(message);
  }
  display.display();
  cardDisplayed = true;
  promptDisplayed = false;
}

void setup() {
  #if ENABLE_SERIAL
  Serial.begin(115200);
  #endif
  Wire.begin();
  delay(50);
  if (!display.begin(SSD1306_SWITCHCAPVCC, SCREEN_ADDRESS)) {
    while (1);
  }

  display.clearDisplay();
  display.setTextColor(SSD1306_WHITE);
  display.setTextSize(2);
  display.setCursor(18, 0);
  display.println("READ MODE");
  display.setTextSize(1);
  display.setCursor(0, 20);
  display.println("Scan Card to Begin...");
  display.display();
  delay(1000);

  loadAuthorizedCards();
  adminUID = loadAdminUID();
  #if ENABLE_SERIAL
  Serial.println("Booting HID RFID Door Simulator (Nano)");
  Serial.print("Loaded "); Serial.print(cardCount); Serial.println(" authorized card(s)");
  Serial.print("Admin UID: "); Serial.println(adminUID);
  Serial.print("Pins - D0:"); Serial.print(WIEGAND_D0_PIN);
  Serial.print(" D1:"); Serial.print(WIEGAND_D1_PIN);
  Serial.print(" BEEPER:"); Serial.print(BEEPER_PIN);
  Serial.print(" SIGNAL:"); Serial.println(SIGNAL_PIN);
  #endif
  displayScanPrompt();

  wg.begin(WIEGAND_D0_PIN, WIEGAND_D1_PIN);

  pinMode(BEEPER_PIN, OUTPUT);
  digitalWrite(BEEPER_PIN, HIGH);
  pinMode(SIGNAL_PIN, OUTPUT);
  digitalWrite(SIGNAL_PIN, LOW);
}
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

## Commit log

2025-05-14 Added Door Simulator code and Cases directory
    [R10_Case_Top.stl, R10_Case_bottom.stl, Rp15_Bottom.stl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]
2025-05-14 Reorganized codebase: Added Arduino nano, ESP32 code directories and Images. Removed old simulator file.
2025-05-14 Updated ESP32 code: Added HID Door Simulator code and data directory, removed Index.html
2025-05-17 Restructure: Rename 'ESP32 Code' to 'ESP32_Code' for better file organization
2025-05-19 Update ESP32 code and reorganize Arduino nano code structure
2025-05-20 Update ESP32 code and add admin configuration
2025-05-20 Update ESP32 code
2025-05-21 Update ESP32 code, README, and add HomeAssistant integration
2025-06-05 Updated ESP32_Code.ino
2025-09-07 Add Admin UID configuration instructions to README and implement Admin UID handling in Arduino code
